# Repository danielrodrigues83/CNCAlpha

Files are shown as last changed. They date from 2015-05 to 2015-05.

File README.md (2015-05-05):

# CNCAlpha
Projeto de uma CNC para Hobby.
Iniciei este projeto com o intuito de facilitar a vida de quem está querendo começar a construir sua primeira máquina CNC.

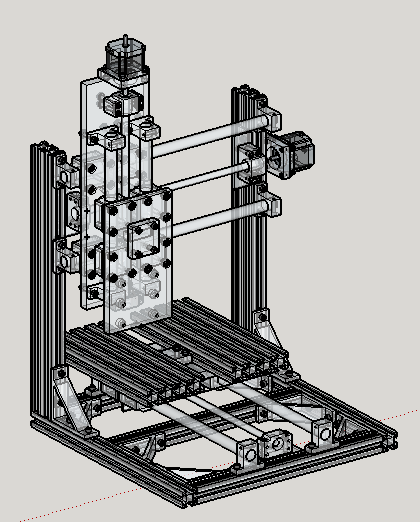
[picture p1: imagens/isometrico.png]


#Objetivos
Criar uma máquina fresadora CNC para hobby que seja capaz de usinar madeira, PCB, acrílico, PVC e demais materiais macios.
Em uma outra etapa pretendo ter um modelo que seja capaz de usinar metais macios, como por exemplo, ligas de Alumínio.

#Especificações
 - Área de trabalho: X 240mm Y 230mm Z 80mm
 - Tensão de trabalho: 24V

#Softwares Utilizados
 - <a href="http://www.sketchup.com/products/sketchup-make" target="_blank">SketchUp Make 14</a>
 - <a href="http://www.3ds.com/products-services/draftsight-cad-software/free-download/" target="_blank">DraftSight V1R3.2</a>
 - <a href="http://www.cambam.info/" target="_blank">CamBam 0.9.4</a>

#Materiais
 As quantidades de materiais estão detalhadas no arquivo <a href="CNCAlpha-BOM.xlsx" target="_blank">CNCAlpha-BOM.xlsx</a>
 - <a href="http://pt.aliexpress.com/item/1204-Rolled-Ballscrew-set-1pcs-SFU1204-L350mm-61mm-machining-parts-1pcs-ballnut-end-machining-1set-BK10/476214507.html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" target="_blank">Fuso de esfera recirculante</a>
 - <a href="http://pt.aliexpress.com/item/Free-shipping-6pcs-SK20-20mm-Shaft-Support-CNC-Router-SH20A/1048914600.html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" target="_blank">SK20</a>
 - <a href="http://pt.aliexpress.com/item/New-4pcs-lot-Free-shipping-SC20UU-SCS20UU-20mm-Linear-Slide-Block-for-DIY-CNC-Router-linear/1267047427.html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" target="_blank">SCS20UU</a>
 - <a href="http://www.marvitubos.com.br/" target="_blank">Eixos lineares 20mm</a>
 - <a href="http://www.aliexpress.com/item/Free-Shipping-6-35mm-8mm-Stepper-Motor-Shaft-Coupler-6-35mmx8mm-flexible-shaft-couplings-3pcs-lot/32241418792.html" target="_blank">Acopladores 6,35x8mm</a>
 - <a href="http://www.casafer.com.br/produto-477-Parafuso+Allen+com+Cabeca+(DIN912)" target="_blank">Parafusos allen cabeça cilíndrica(DIN912)</a>
 - <a href="http://www.lojaforseti.com/produtos-index/categorias/1167688/perfil.html" target="_blank">Perfis de Alumínio 30x30mm e 30x60mm</a> 
 - <a href="http://www.lojaforseti.com/produtos-index/categorias/1434667/cantoneiras.html" target="_blank">Cantoneiras</a> 
 - <a href="http://www.lojaforseti.com/produtos-index/categorias/1506114/porcas.html" target="_blank">Porcas para os perfis de alumínio</a> 
 - <a href="http://www.aliexpress.com/item/Free-shipping-CNC-3-AXIS-Stepper-Driver-Board-Controller-TB6560-3-5A-SM362-CF/520301796.html" target="_blank">Placa controladora de 3 eixos</a>
 - <a href="http://www.aliexpress.com/store/product/3PCS-NEMA23-270-Oz-in-CNC-stepper-motor-stepping-motor-3-0A/907217_541699816.html" target="_blank">Motores Nema 23</a>
 - <a href="http://produto.mercadolivre.com.br/MLB-651414629-fonte-chaveada-12v-30a-360w-bivolt-p-cameras-fita-led-cftv-_JM" target="_blank">Fonte 12V 30A</a>
 - <a href="http://www.soldafria.com.br/chave-micro-switch-c-30_267.html" target="_blank">Endstops, fios</a>
 - <a href="http://www.aliexpress.com/item/2pcs-CNC-Emergency-Stop-Pushbutton-Switch-LAY37-11ZS/32331147402.html" target="_blank">Botão de emergência</a>
 - <a href="http://www.ebay.com/itm/ER11-Spindle-for-Sable-2015-SPD-ER11-ENGRAVER-mill-PCBs-engraving-/201337995174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" target="_blank">Spindle</a>

#Instruções para fabricação
 Os arquivos contendo os desenhos das peças que precisam ser fabricadas estão na pasta <a href="desenhos2D" target="_blank">desenho2D</a>.
 O objetivo é utilizar estes arquivos como base para a criação dos Gcodes, por isso não foram incluídos cotas e símbolos.
 Os arquivos Gcodes serão salvos na pasta <a href="cam" target="_blank">cam</a>
 Serão disponibilizados, também, os arquivos editáveis do CamBam.
 
#Observações
 - Tentei fazer todas as peças a serem fabricadas com o dimensional que fosse possível usinar através dela.
 - A mesa do eixo Y, devido ao seu tamanho, foi necessário realizar a usinagem em duas etapas.
 - Serão utilizadas duas fontes, ligadas em série, de 12V 30A para fornecer 24V aos motores e ao spindle.
 - Estou tentando fazer algo organizado e que seja útil para quem queira iniciar neste hobby, portanto qualquer ajuda e sugestão construtiva são muito bem vindos.

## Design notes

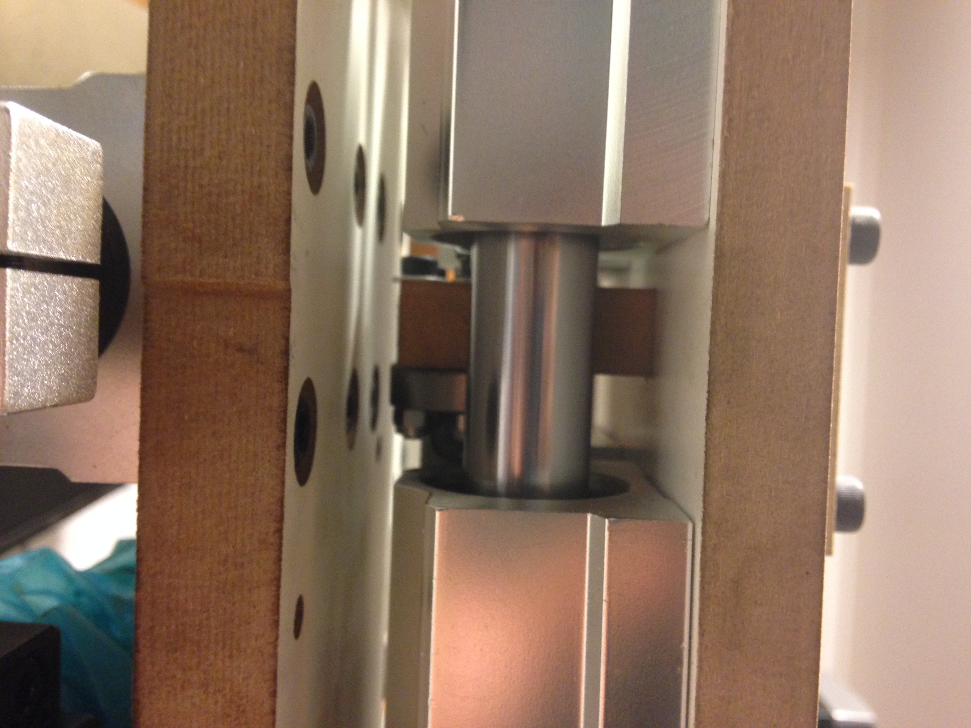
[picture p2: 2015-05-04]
fotos/2015-04-30 17.04.00.jpg

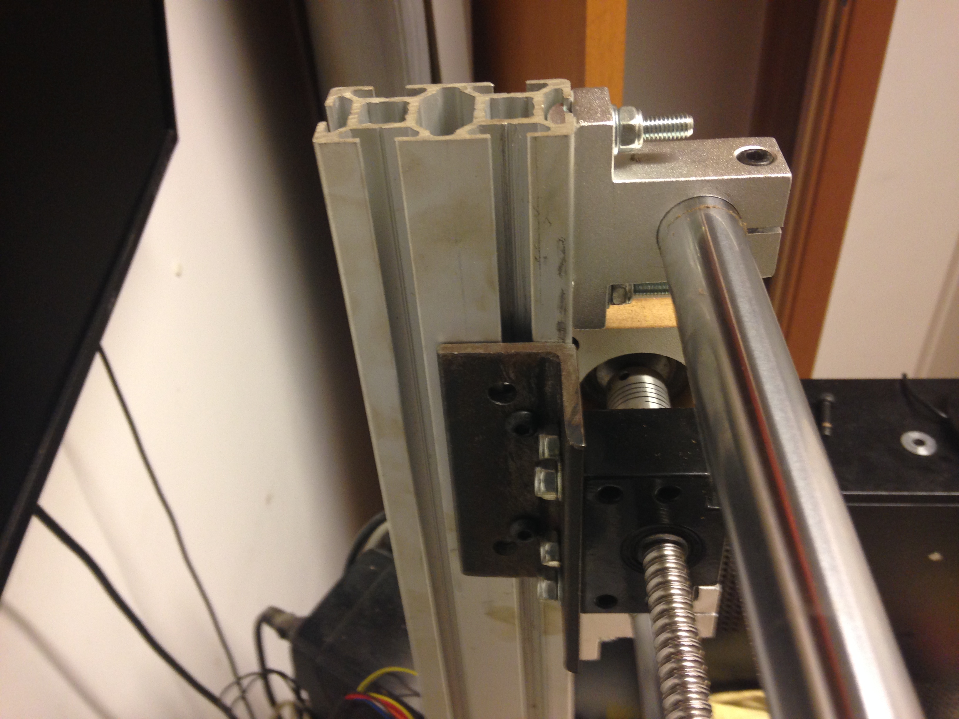
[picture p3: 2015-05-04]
fotos/2015-04-30 17.04.11.jpg

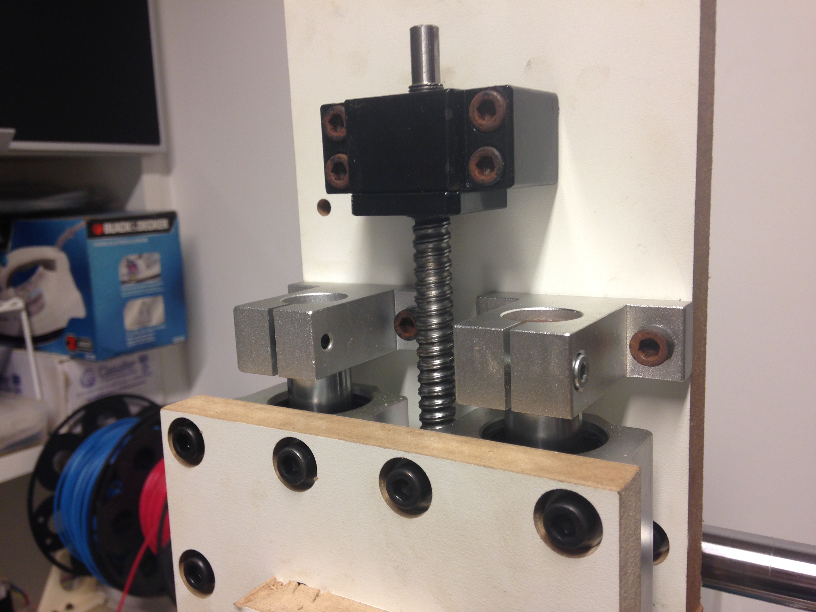
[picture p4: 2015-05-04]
fotos/2015-04-30 17.03.50.jpg

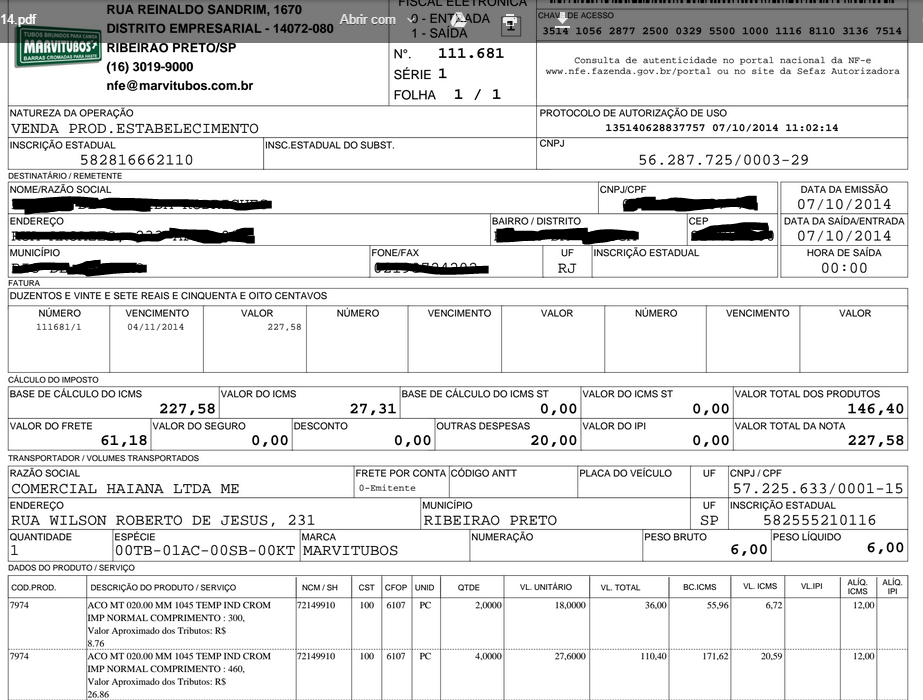
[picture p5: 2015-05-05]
imagens/nota-fiscal-marvitubos.PNG

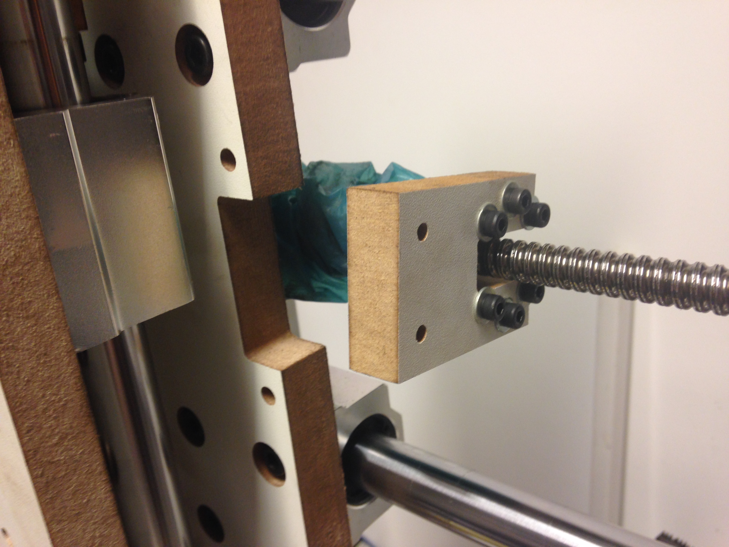
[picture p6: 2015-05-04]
fotos/2015-04-30 17.03.44.jpg

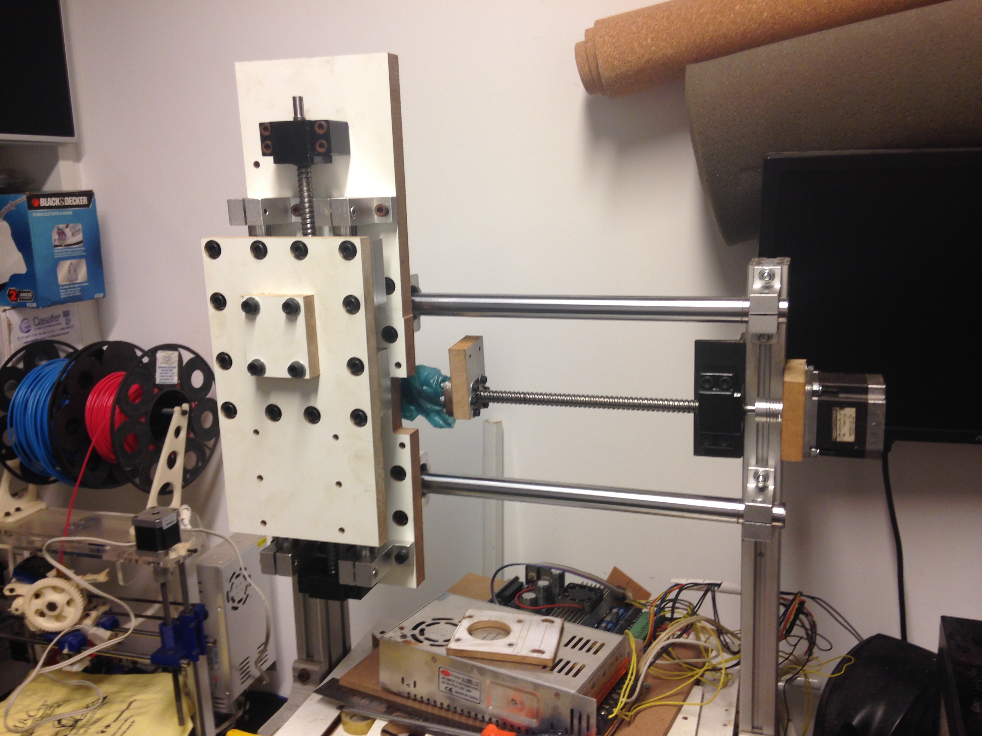
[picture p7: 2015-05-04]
fotos/2015-04-30 17.03.37.jpg

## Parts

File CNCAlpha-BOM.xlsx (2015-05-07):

Lista de Materiais
 | Item | Quantidade | Local | Valor China | Valor Brasil | valor(menor) referencia | valor referencia total | valor Brasil Total
Movimento
 | BF10 | 3 |  |  |  | R$0.00
 | BK10 | 3 |  |  |  | R$0.00
 | Fuso com castanha SFU1204 30cm | 3 | CHINA | R$235.00 | R$320.00 | R$235.00 | R$705.00 | R$960.00
 | SCS20UU | 12 | CHINA | R$20.00 | R$40.00 | R$20.00 | R$240.00 | R$480.00
 | SK20 | 12 | CHINA | R$8.50 | R$24.00 | R$8.50 | R$102.00 | R$288.00
 | Eixo diametro 20mm compr. 450mm | 4 | BRASIL |  | R$27.60 | R$27.60 | R$110.40 | R$110.40
 | Eixo diametro 20mm compr. 300mm | 2 | BRASIL |  | R$27.98 | R$27.98 | R$55.96 | R$55.96
 | Acoplador eixos 6,35 x 8mm x 25mm | 3 | CHINA | R$15.00 | R$15.00 | R$15.00 | R$45.00 | R$45.00
Estrutura
 | cantoneira100x100x30 | 8 | BRASIL |  | R$13.00 | R$13.00 | R$104.00 | R$104.00
 | Perfil T-slot 30x30 compr. 400mm | 3 | BRASIL |  | R$11.20 | R$11.20 | R$33.60 | R$33.60
 | Perfil T-slot 30x30 compr. 460mm | 2 | BRASIL |  | R$12.88 | R$12.88 | R$25.76 | R$25.76
 | Perfil T-slot 60x30 compr. 500mm | 2 | BRASIL |  | R$24.00 | R$24.00 | R$48.00 | R$48.00
 | Perfil T-slot 60x30 compr. 300mm | 4 | BRASIL |  | R$14.40 | R$14.40 | R$57.60 | R$57.60
Parafusos
 | DIN912 M4X30+NYLOC | 18 | BRASIL |  | R$0.70 | R$0.70 | R$12.60 | R$12.60
 | DIN912 M5X20+NYLOC | 12 | BRASIL |  | R$0.70 | R$0.70 | R$8.40 | R$8.40
 | DIN 912 M6x10 | 8 | BRASIL |  | R$0.70 | R$0.70 | R$5.60 | R$5.60
 | DIN 912 M6x16 | 60 | BRASIL |  | R$0.70 | R$0.70 | R$42.00 | R$42.00
 | DIN 912 M6x20+ARRUELA | 32 | BRASIL |  | R$0.70 | R$0.70 | R$22.40 | R$22.40
 | DIN 912 M6x25+ARRUELA+NYLOC | 2 | BRASIL |  | R$0.70 | R$0.70 | R$1.40 | R$1.40
 | DIN 912 M6x35+ARRUELA+NYLOC | 12 | BRASIL |  | R$0.70 | R$0.70 | R$8.40 | R$8.40
 | DIN912 M6X40+ARRUELA+NYLOC | 12 | BRASIL |  | R$0.70 | R$0.70 | R$8.40 | R$8.40
 | DIN912 M6X40 | 4 | BRASIL |  | R$0.70 | R$0.70 | R$2.80 | R$2.80
 | DIN912 M6X50+ARRUELA+NYLOC | 6 | BRASIL |  | R$0.70 | R$0.70 | R$4.20 | R$4.20
 | Porca para Perfil T-slot 30 - M6 | 72 | BRASIL |  | R$1.65 | R$1.65 | R$118.80 | R$118.80
Fabricação
 | Fabricar-cantoneira-1/2" | 1 | BRASIL |  | R$5.00 | R$5.00 | R$5.00 | R$5.00
 | Fabricar-cantoreira-1/8"x1.1/2"x100-furo-duplo | 2 | BRASIL |  | R$20.00 | R$20.00 | R$40.00 | R$40.00
 | Fabricar-cantoreira-1/8"x1.1/2"x100-furo-simples | 2 | BRASIL |  | R$20.00 | R$20.00 | R$40.00 | R$40.00
 | Fabricar-X-mesa | 1 | BRASIL |  | em cotação | em cotação
 | Fabricar-X-trava-castanha-2 | 1 | BRASIL |  | em cotação | em cotação
 | Fabricar-X-trava-castanha | 1 | BRASIL |  | em cotação | em cotação
 | Fabricar-Y-trava-castanha | 1 | BRASIL |  | em cotação | em cotação
 | Fabricar-Z-mesa | 1 | BRASIL |  | em cotação | em cotação
 | Fabricar-Z-trava-castanha-2 | 1 | BRASIL |  | em cotação | em cotação
 | Fabricar-Z-trava-castanha | 1 | BRASIL |  | em cotação | em cotação
 | Fabricar-suporte-motor-XY | 2 | BRASIL |  | em cotação | em cotação
 | Fabricar-suporte-motor-Z | 1 | BRASIL |  | em cotação | em cotação
 | Fabricar-Y-mesa | 1 | BRASIL |  | em cotação | em cotação
Eletrônica
 | Motores Nema 23 15Kgf*cm | 3 | CHINA | R$135.00 | R$60.00 | R$135.00 | R$405.00 | R$180.00
 | Placa controladora de 3eixos TB6560 | 1 | CHINA | R$125.00 | R$280.00 | R$125.00 | R$125.00 | R$280.00
 | Fonte 12v 30A | 2 | BRASIL |  | R$57.00 | R$57.00 | R$114.00 | R$114.00
 | End stop switch | 6 | BRASIL |  | R$5.00 | R$5.00 | R$30.00 | R$30.00
 | Botao de parada | 1 | CHINA | R$25.00 | R$17.00 | R$17.00 | R$17.00 | R$17.00
 | Spindle | 1 | CHINA | R$305.00 | R$350.00 | R$305.00 | R$305.00 | R$350.00
 |  |  |  |  |  | TOTAL | R$2843.32 | R$3499.32

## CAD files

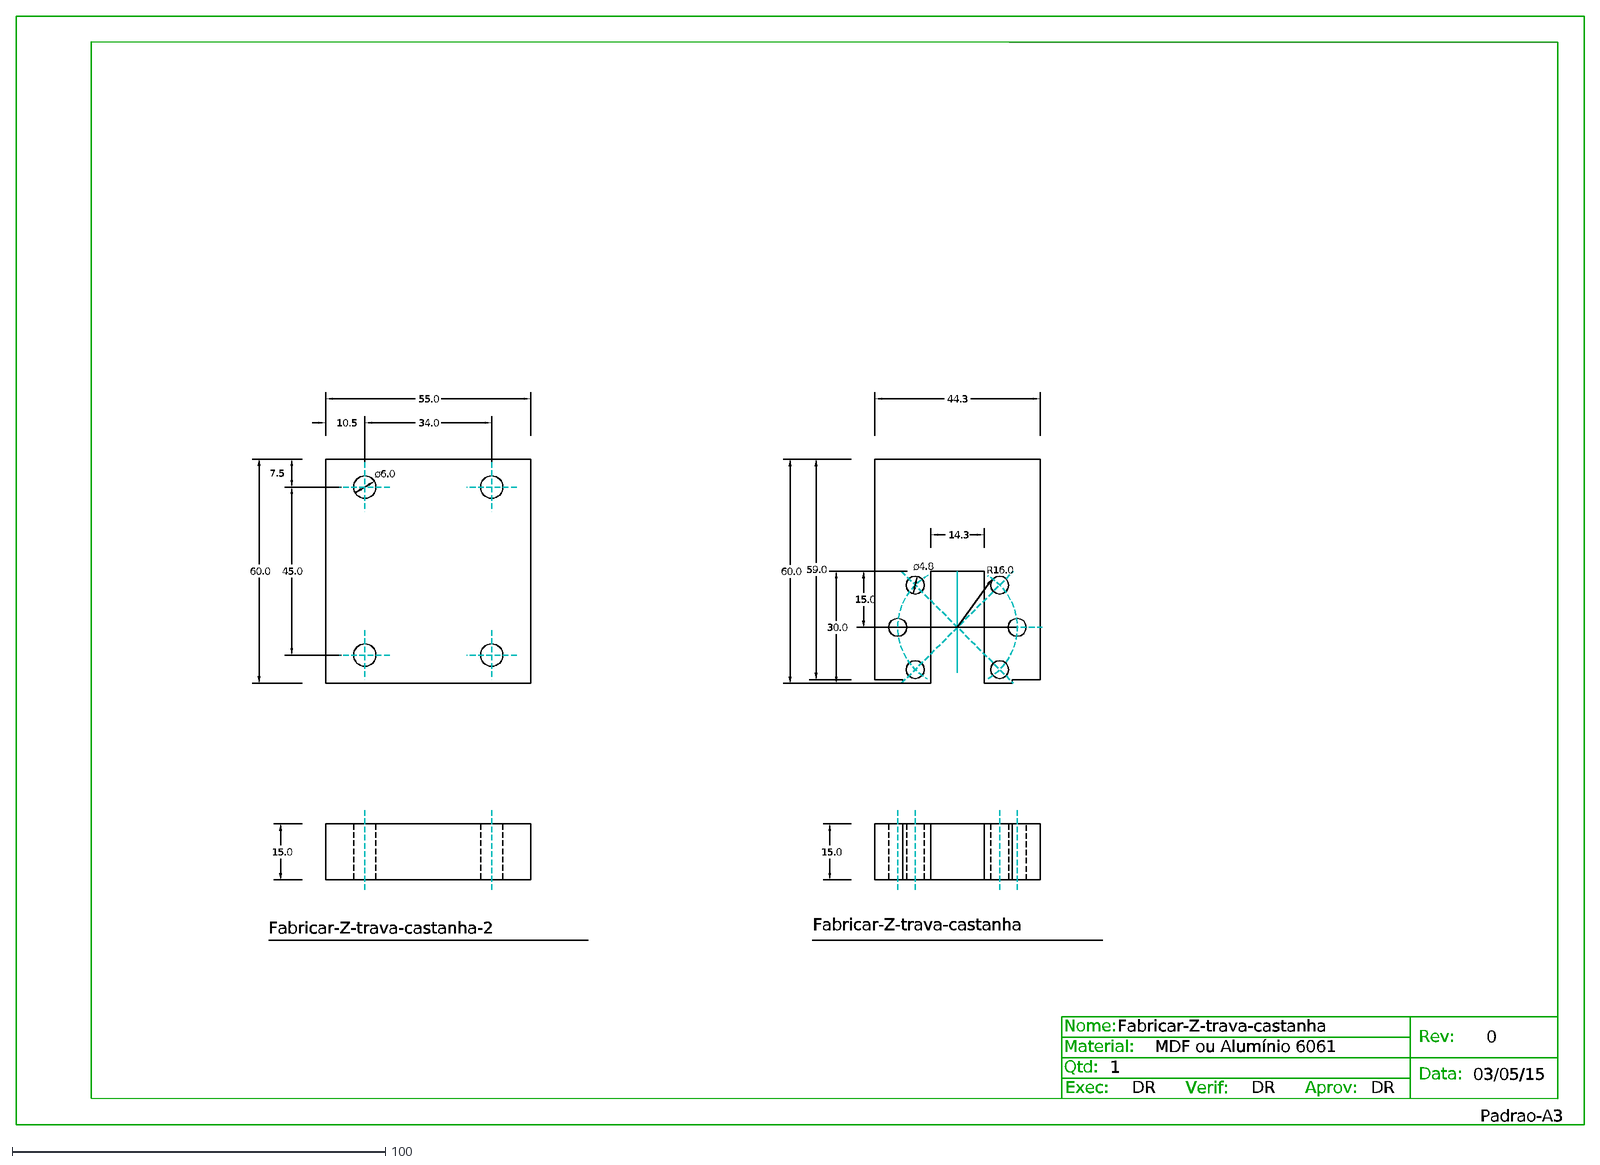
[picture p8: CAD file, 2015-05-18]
desenhos2D/Fabricar-Z-trava-castanha.dxf
Padrao-A3
Fabricar-Z-trava-castanha-2
Fabricar-Z-trava-castanha
Verif:
Exec:
Material:
Rev:
Data:
Aprov:
DR
0
03/05/15
MDF ou Alumínio 6061
Nome:
Qtd:
1
R16.0
14.3
60.0
59.0
30.0
15.0
44.3
55.0
10.5
34.0
7.5
45.0
ø4.8
ø6.0

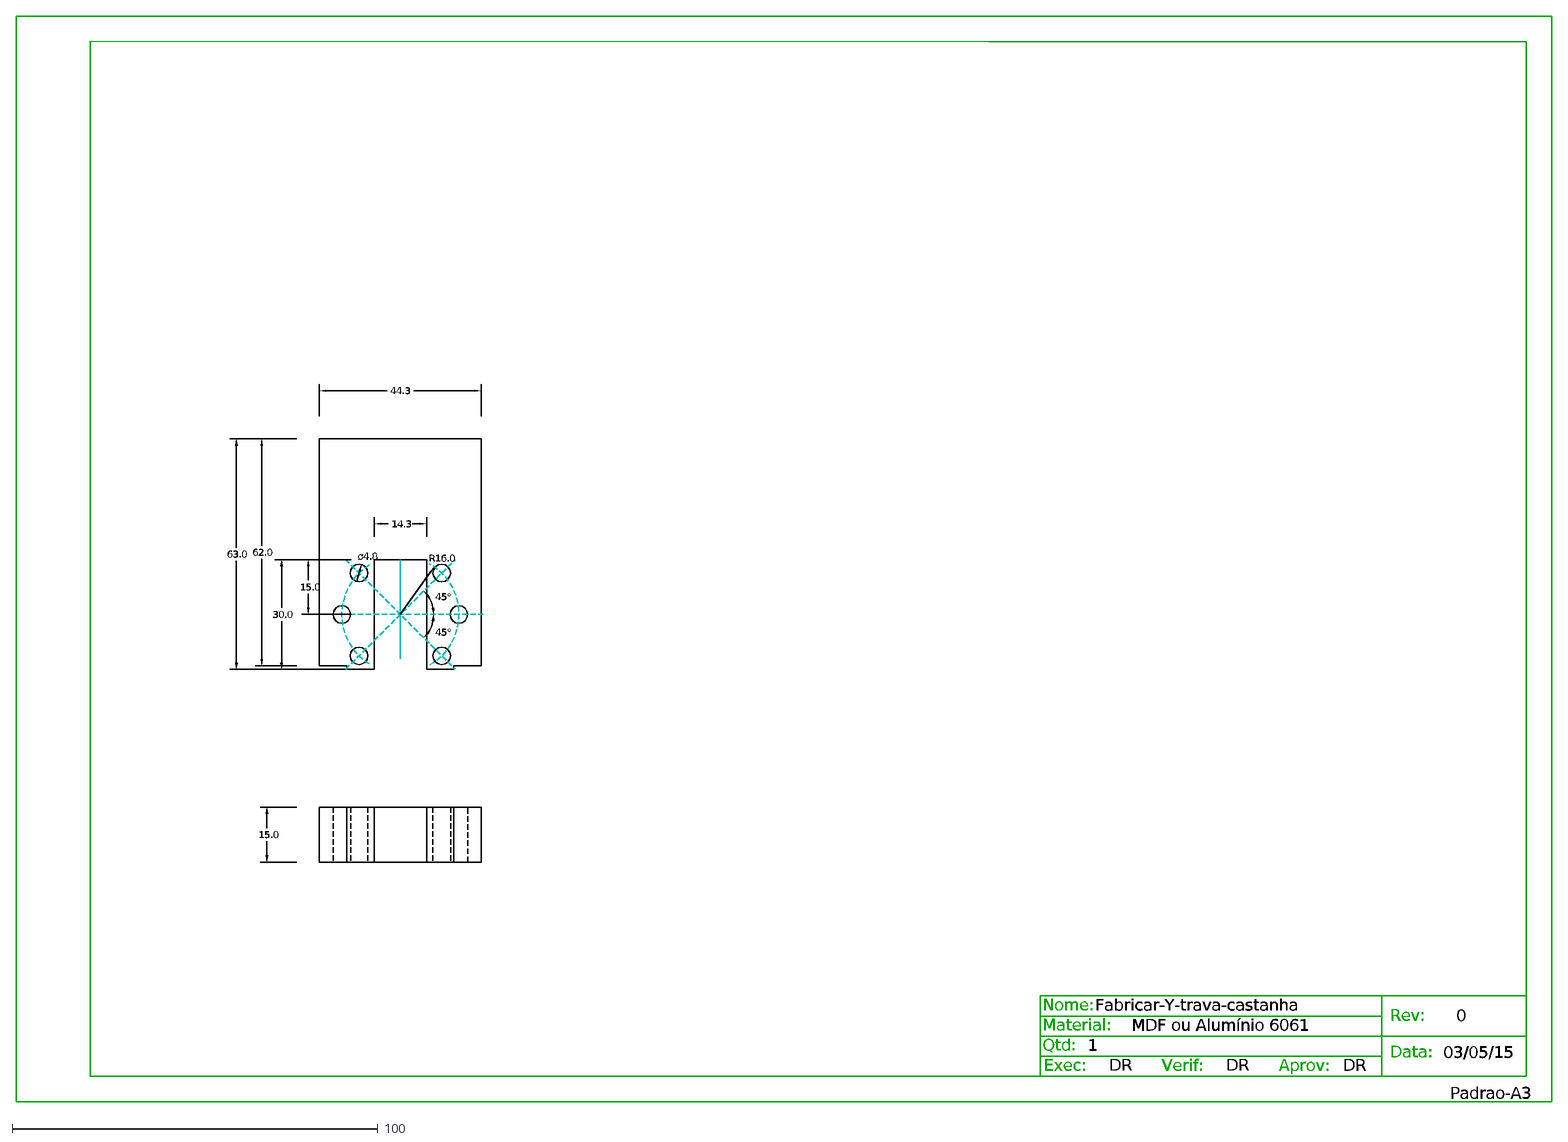
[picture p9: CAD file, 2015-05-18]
desenhos2D/Fabricar-Y-trava-castanha.dxf
Padrao-A3
Verif:
Exec:
Material:
Rev:
Data:
Aprov:
DR
0
03/05/15
MDF ou Alumínio 6061
Fabricar-Y-trava-castanha
Nome:
Qtd:
1
44.3
63.0
62.0
30.0
14.3
45°
R16.0
ø4.8
15.0

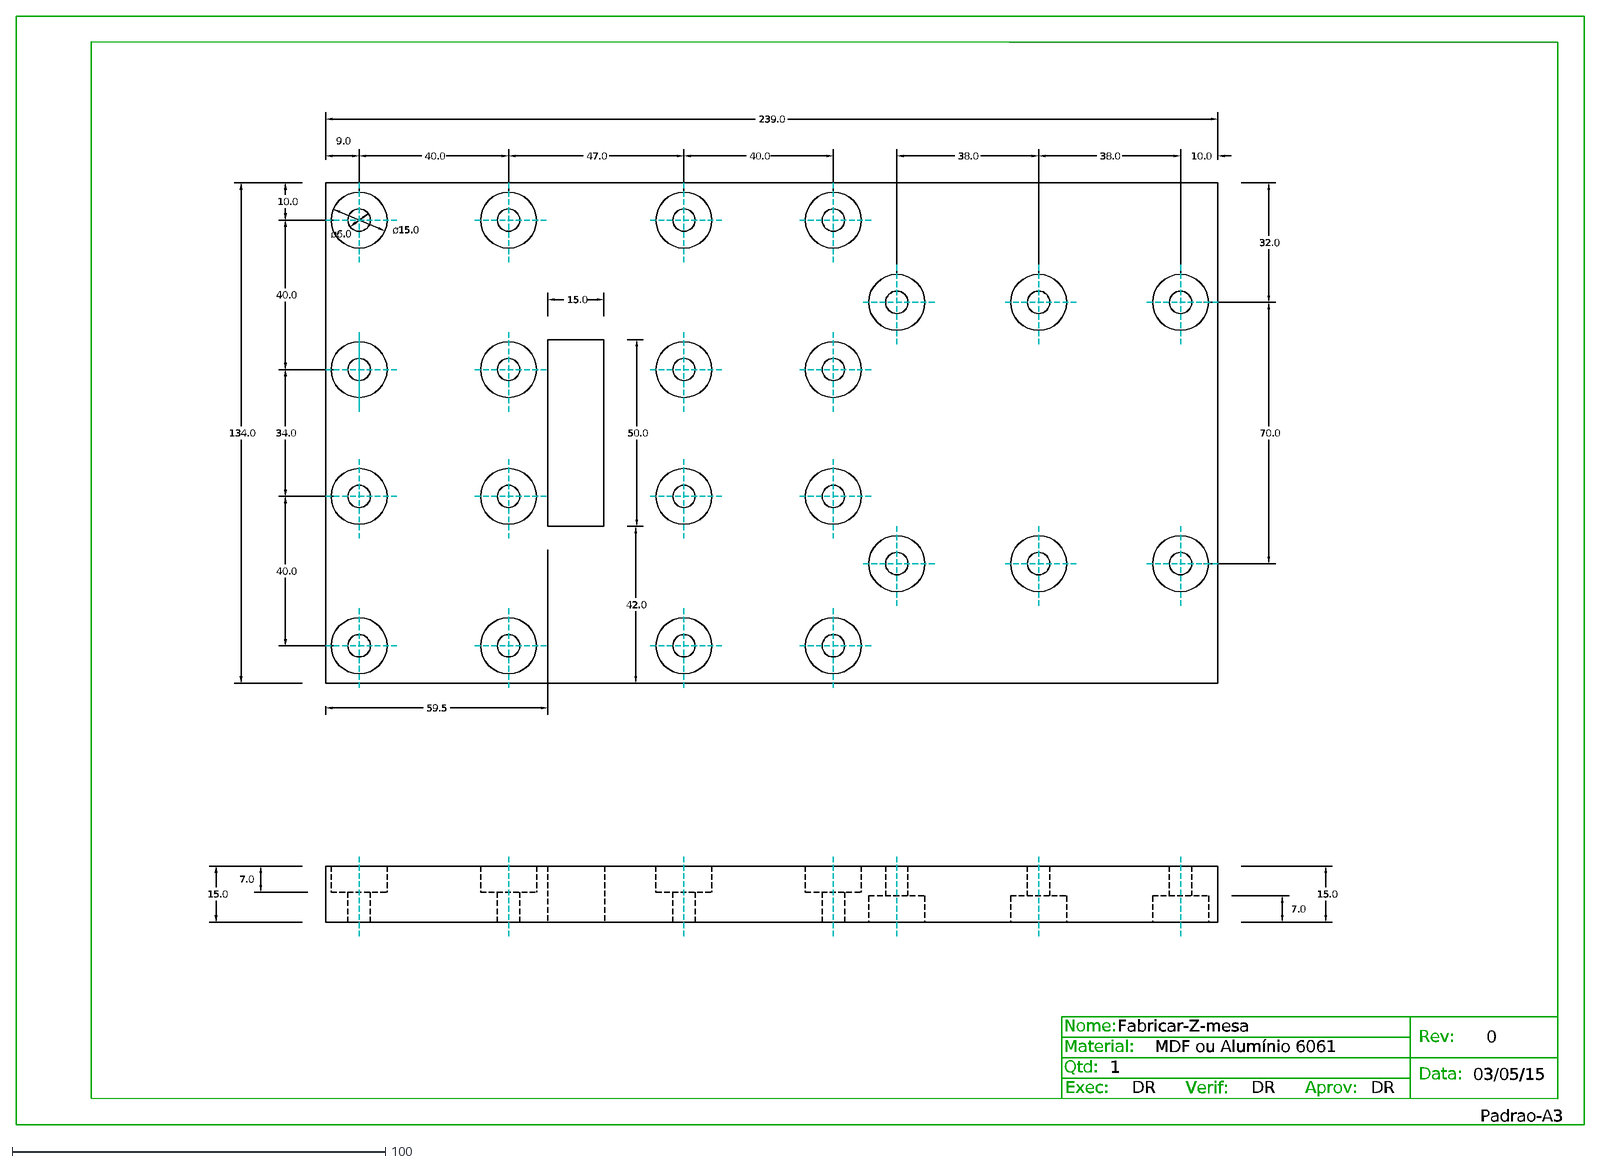
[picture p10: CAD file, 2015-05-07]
desenhos2D/Fabricar-Z-mesa.dxf
Padrao-A3
Verif:
Exec:
Material:
Rev:
Data:
Aprov:
DR
0
03/05/15
MDF ou Alumínio 6061
Fabricar-Z-mesa
Nome:
Qtd:
1
9.0
40.0
47.0
10.0
34.0
50.0
15.0
ø6.0
ø15.0
239.0
134.0
59.5
42.0
38.0
32.0
70.0
7.0

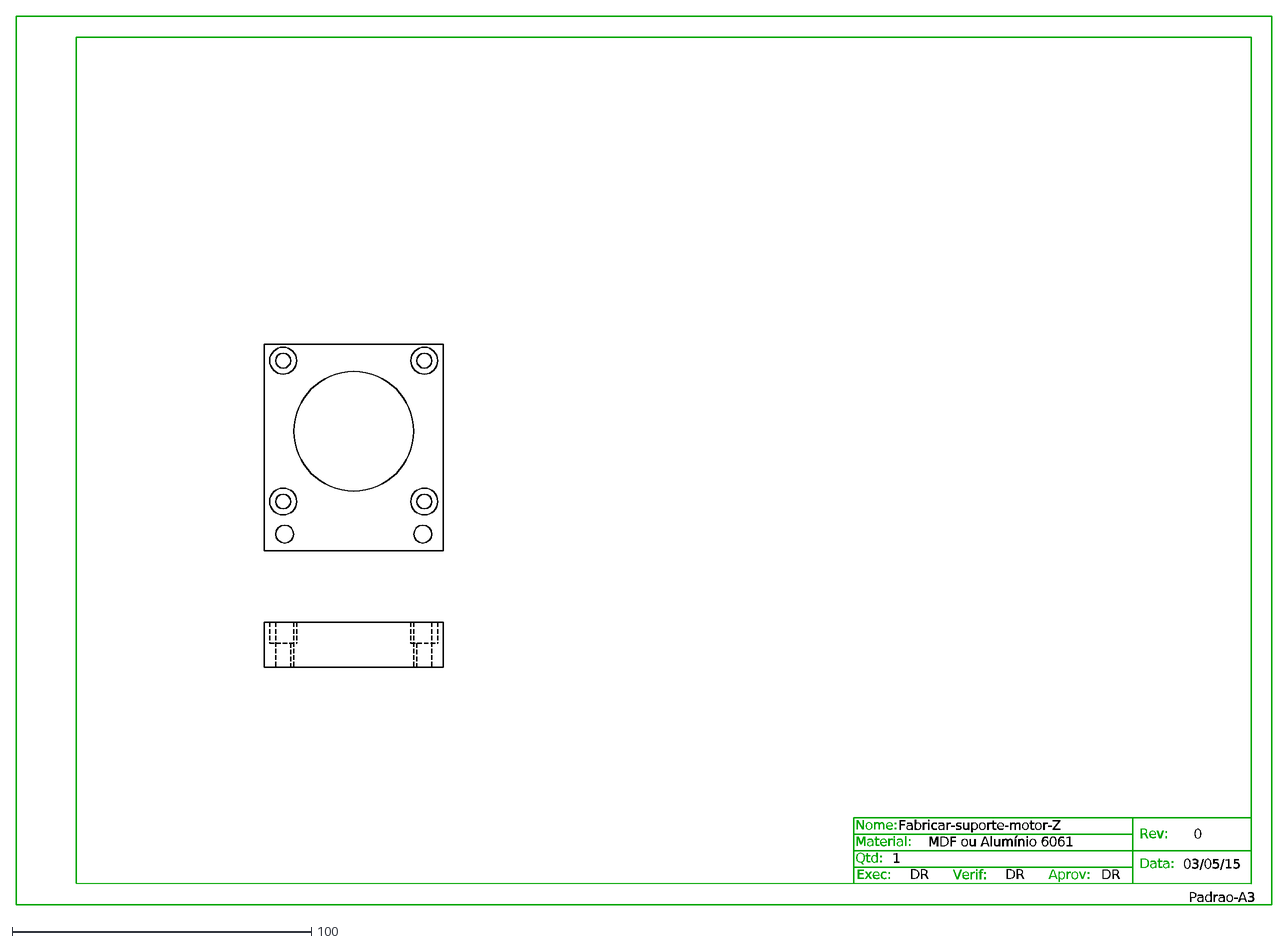
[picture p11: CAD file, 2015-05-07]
desenhos2D/Fabricar-suporte-motor-Z.dxf
Padrao-A3
Verif:
Exec:
Material:
Rev:
Data:
Aprov:
DR
0
03/05/15
MDF ou Alumínio 6061
Fabricar-suporte-motor-Z
Nome:
Qtd:
1

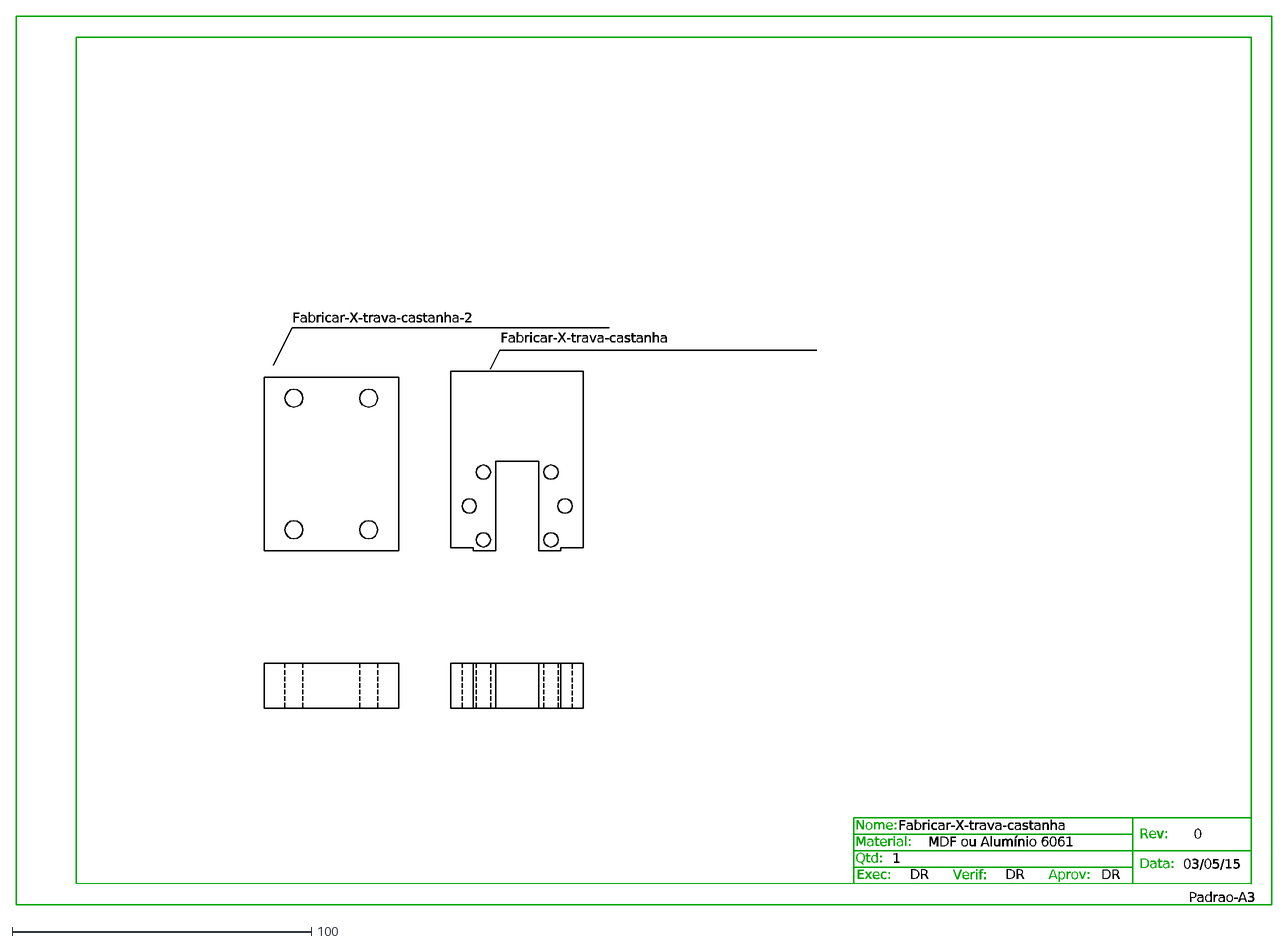
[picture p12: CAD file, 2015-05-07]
desenhos2D/Fabricar-X-trava-castanha.dxf
Padrao-A3
Fabricar-X-trava-castanha-2
Fabricar-X-trava-castanha
Verif:
Exec:
Material:
Rev:
Data:
Aprov:
DR
0
03/05/15
MDF ou Alumínio 6061
Nome:
Qtd:
1

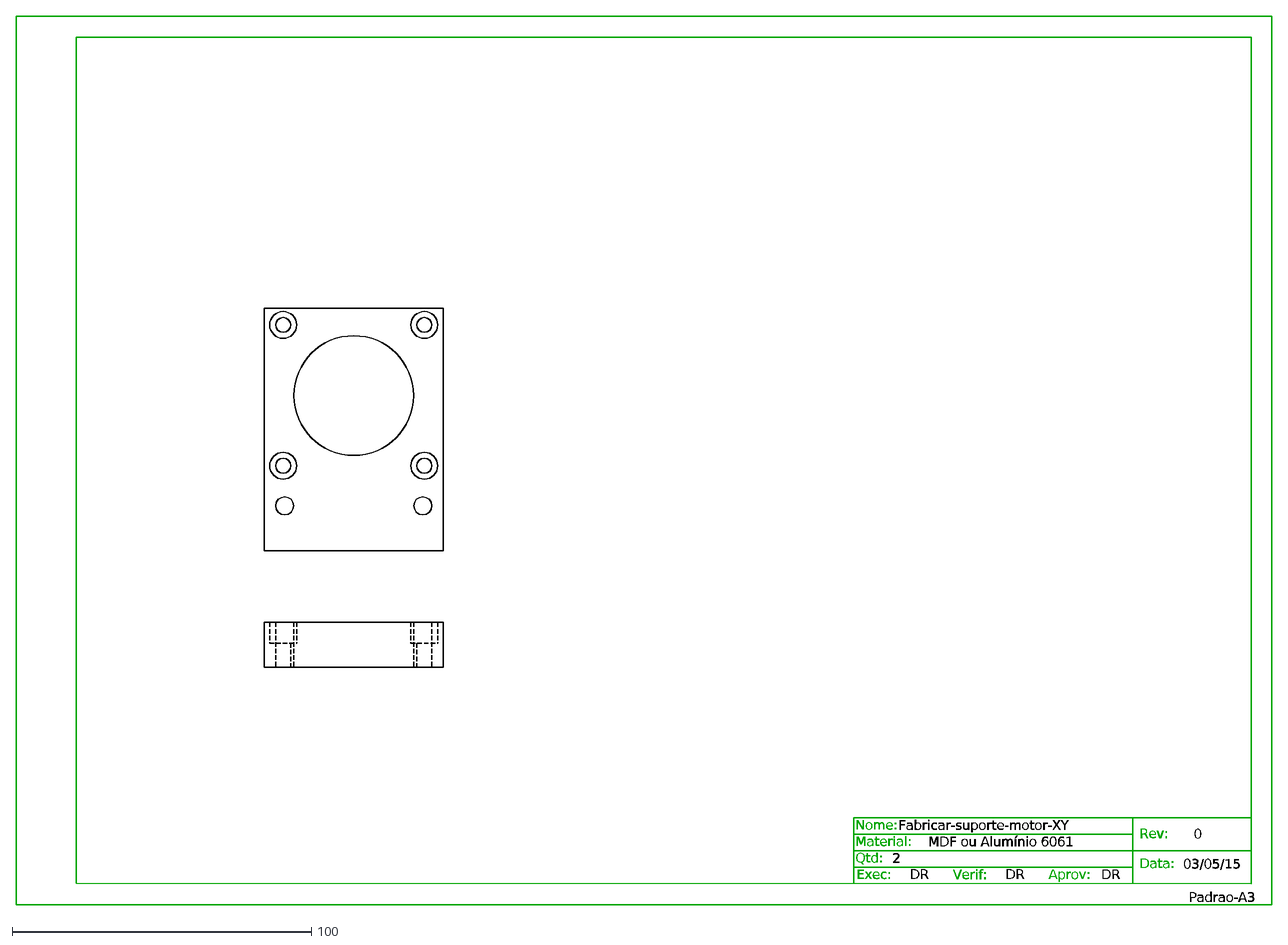
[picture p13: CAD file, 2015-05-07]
desenhos2D/Fabricar-suporte-motor-XY.dxf
Verif:
Exec:
Material:
Rev:
Data:
Aprov:
DR
0
03/05/15
MDF ou Alumínio 6061
Padrao-A3
Fabricar-suporte-motor-XY
Nome:
Qtd:
2

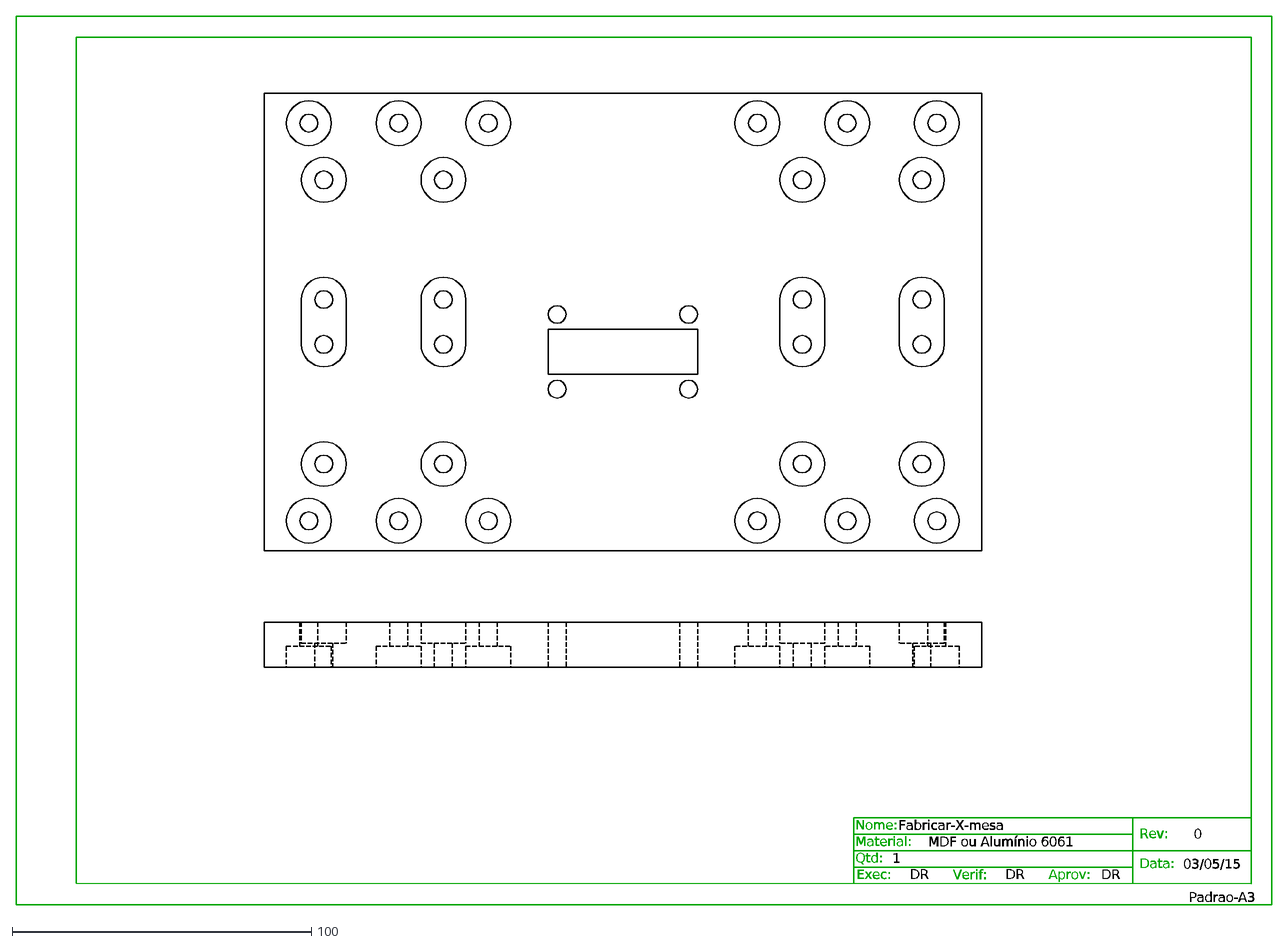
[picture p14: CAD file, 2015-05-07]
desenhos2D/Fabricar-X-mesa.dxf
Padrao-A3
0
Verif:
Exec:
Material:
Rev:
Data:
Aprov:
DR
03/05/15
MDF ou Alumínio 6061
Fabricar-X-mesa
Nome:
Qtd:
1

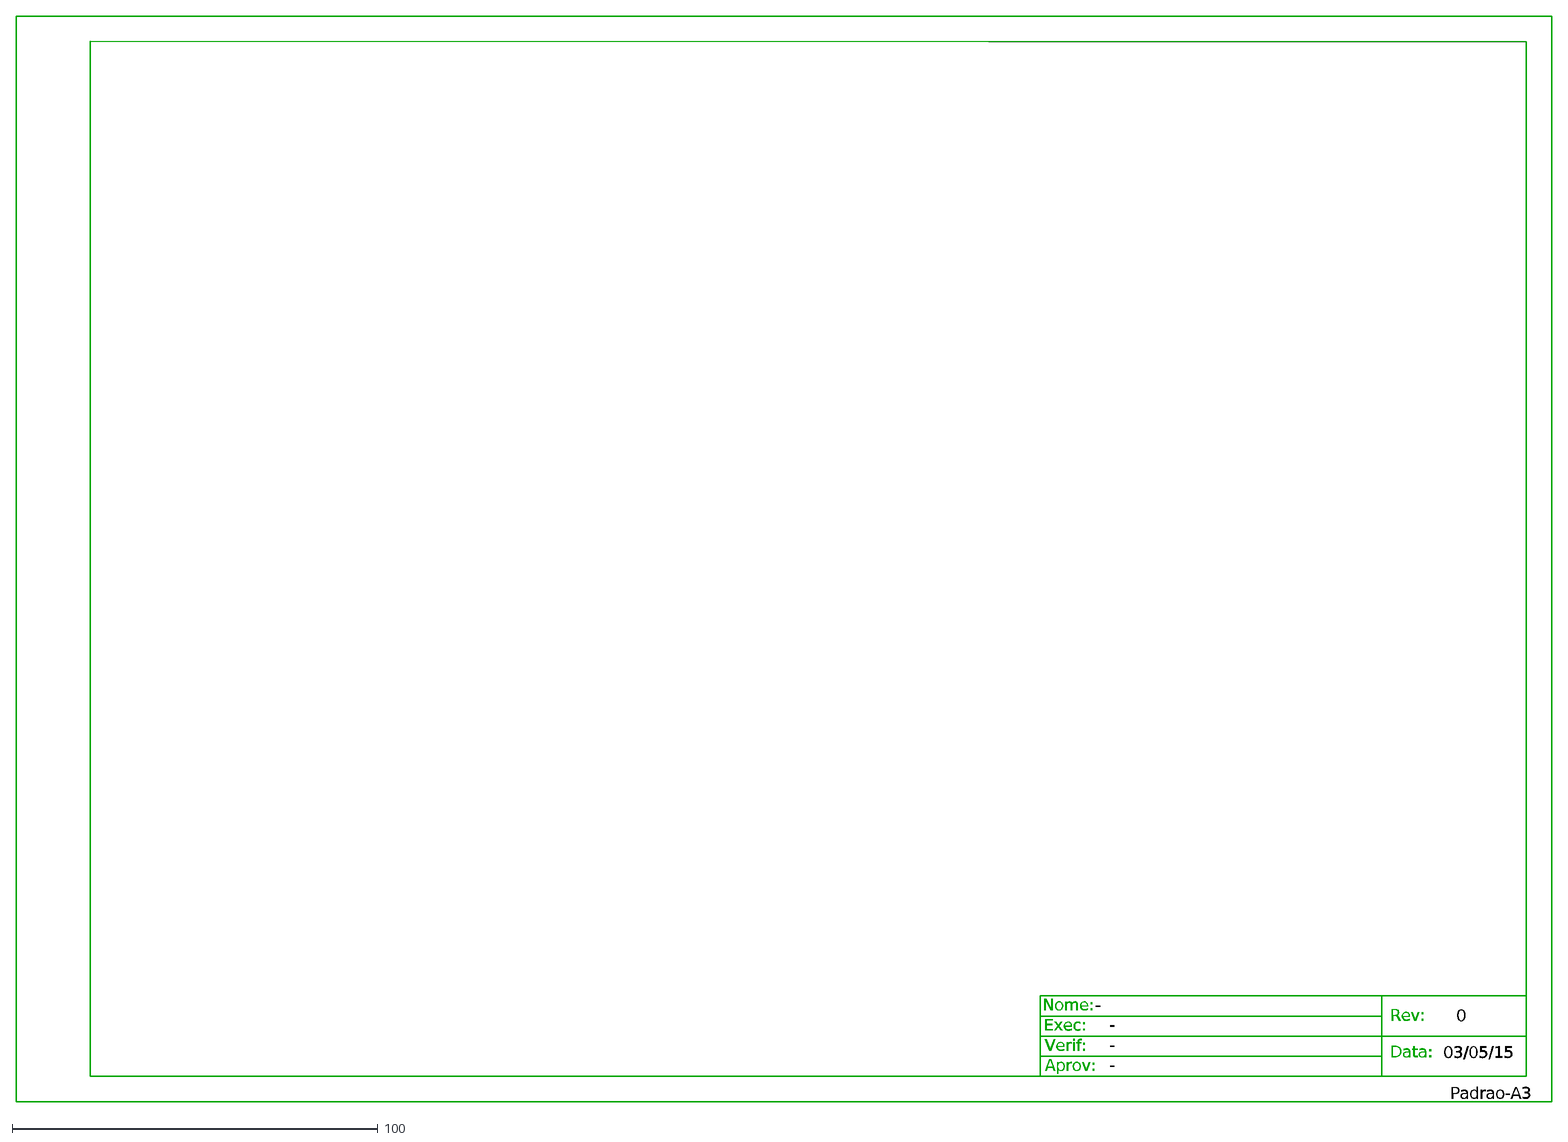
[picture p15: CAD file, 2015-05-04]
desenhos2D/Padrao-A3.dxf
Verif:
Exec:
Nome:
Rev:
Data:
Aprov:
-
0
03/05/15
Padrao-A3

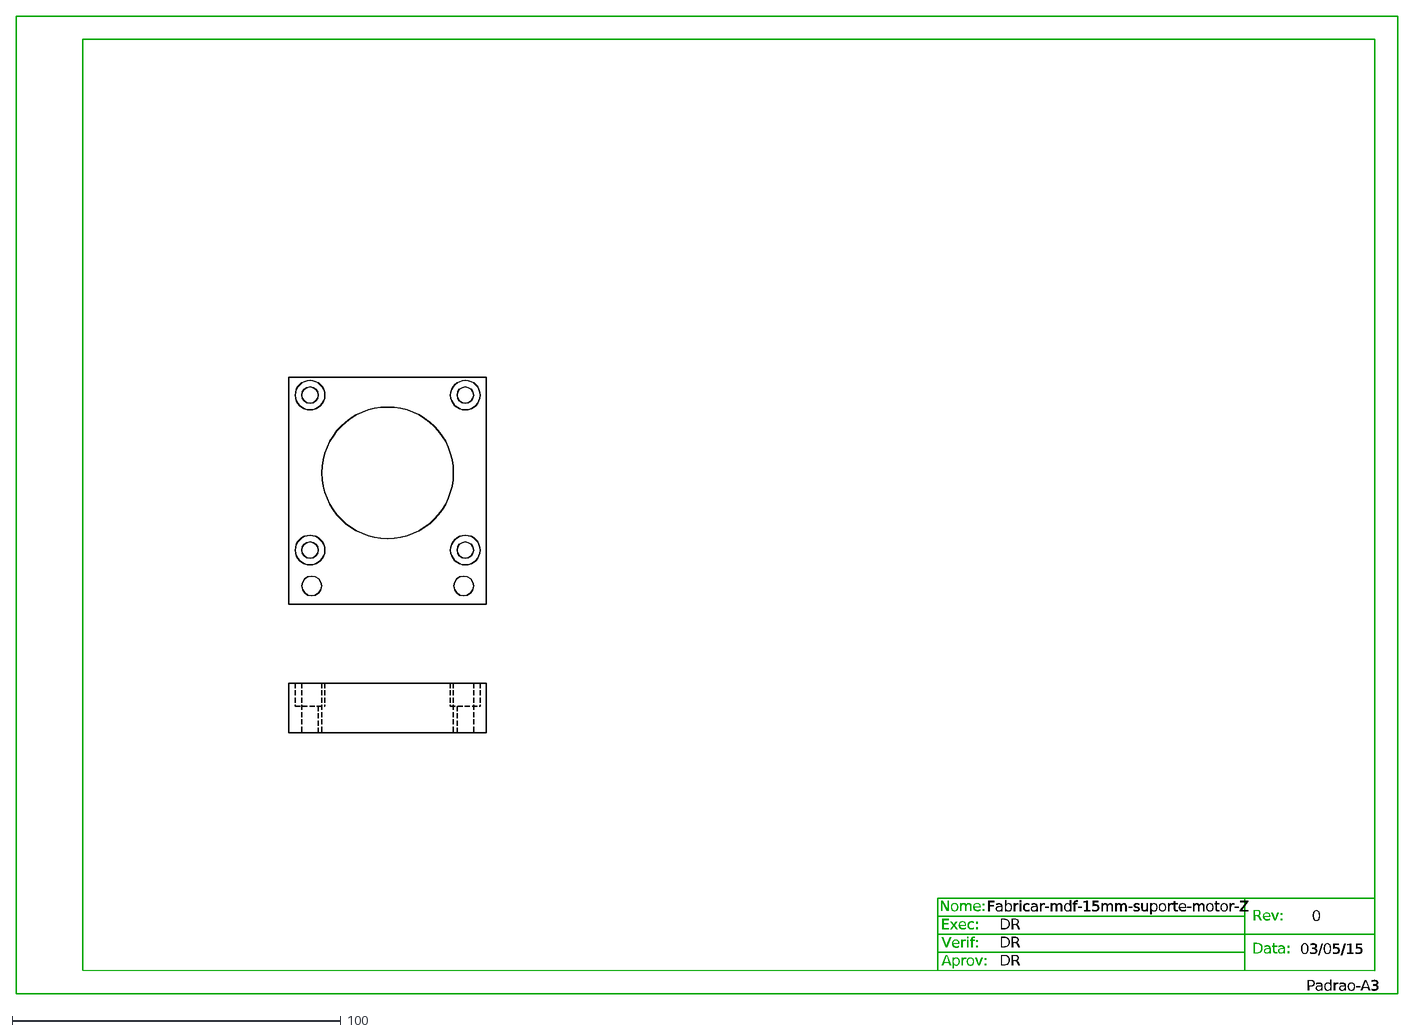
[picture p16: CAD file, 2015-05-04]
desenhos2D/Fabricar-mdf-15mm-suporte-motor-Z.dxf
Verif:
Exec:
Nome:
Rev:
Data:
Aprov:
DR
0
03/05/15
Fabricar-mdf-15mm-suporte-motor-Z
Padrao-A3

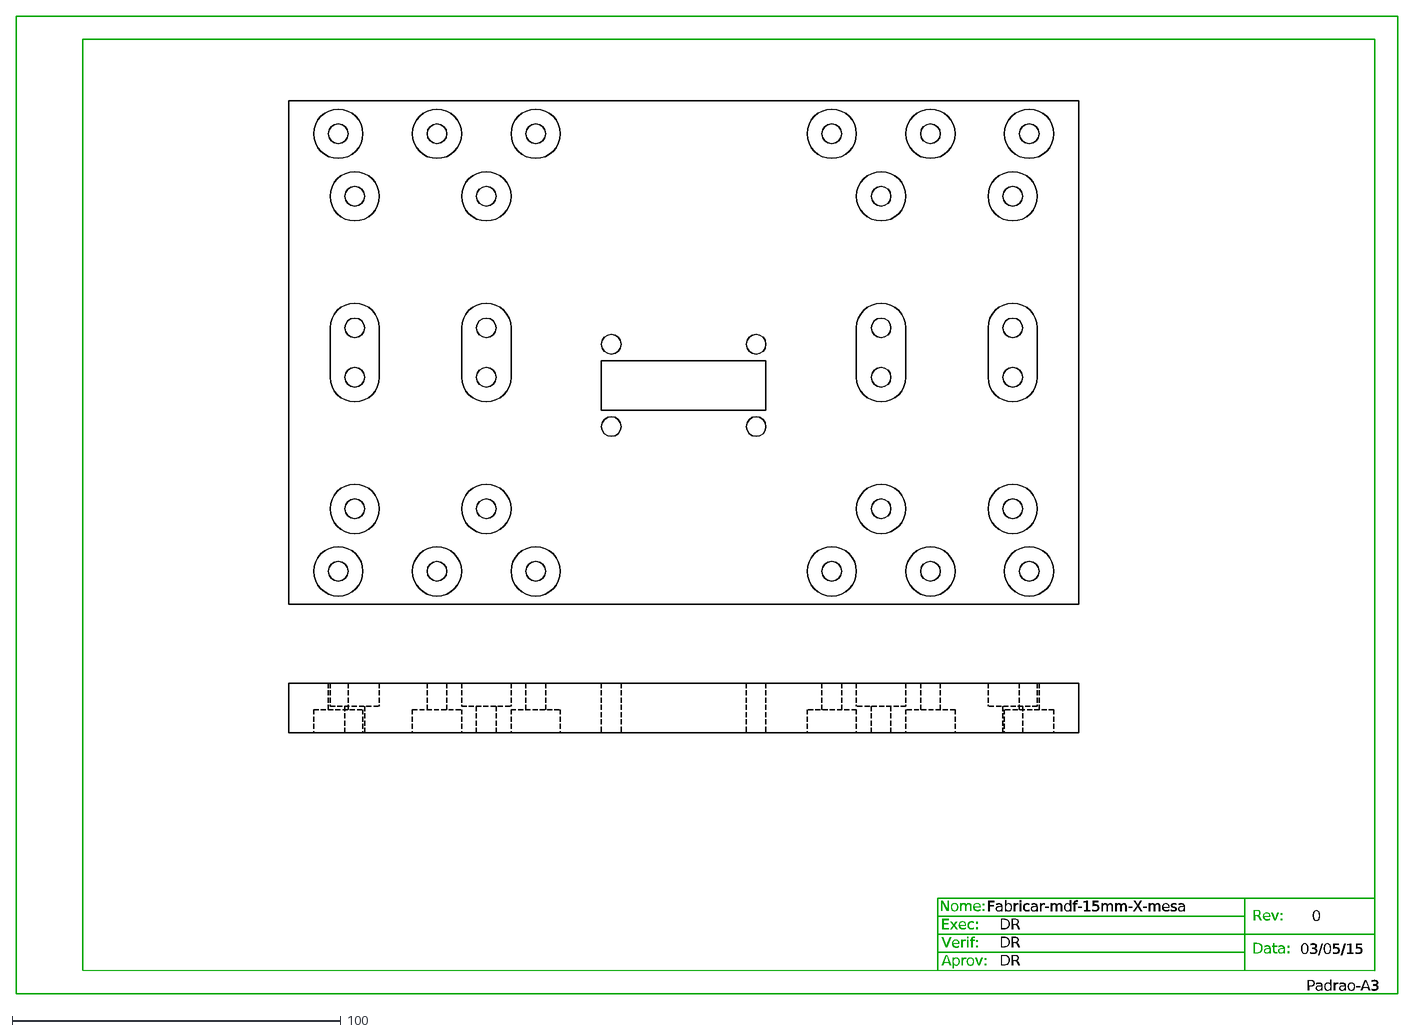
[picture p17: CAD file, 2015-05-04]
desenhos2D/Fabricar-mdf-15mm-X-mesa.dxf
Verif:
Exec:
Nome:
Rev:
Data:
Aprov:
DR
0
03/05/15
Fabricar-mdf-15mm-X-mesa
Padrao-A3

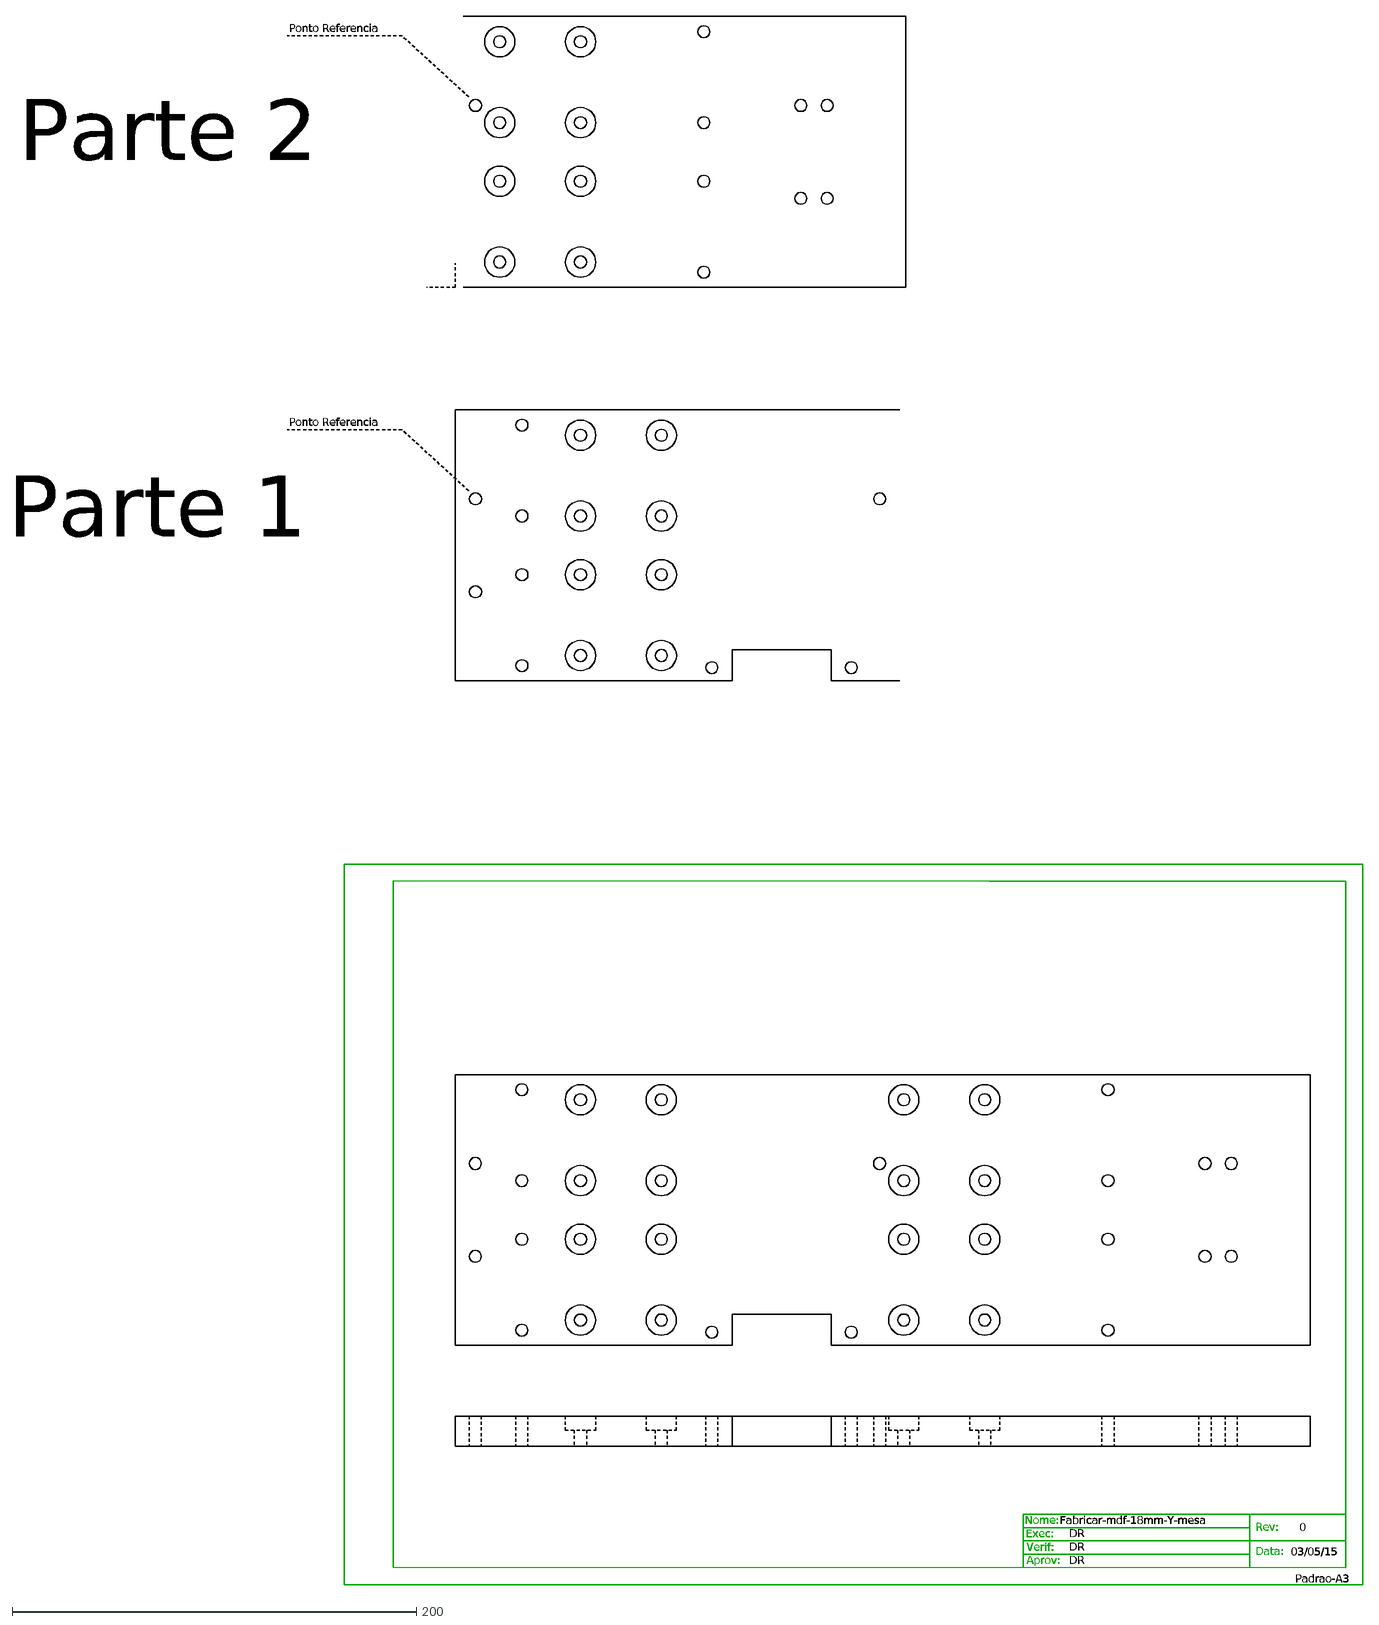
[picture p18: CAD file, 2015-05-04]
desenhos2D/Fabricar-mdf-18mm-Y-mesa.dxf
Verif:
Exec:
Nome:
Rev:
Data:
Aprov:
DR
0
03/05/15
Fabricar-mdf-18mm-Y-mesa
Padrao-A3
Parte 1
Parte 2
Ponto Referencia

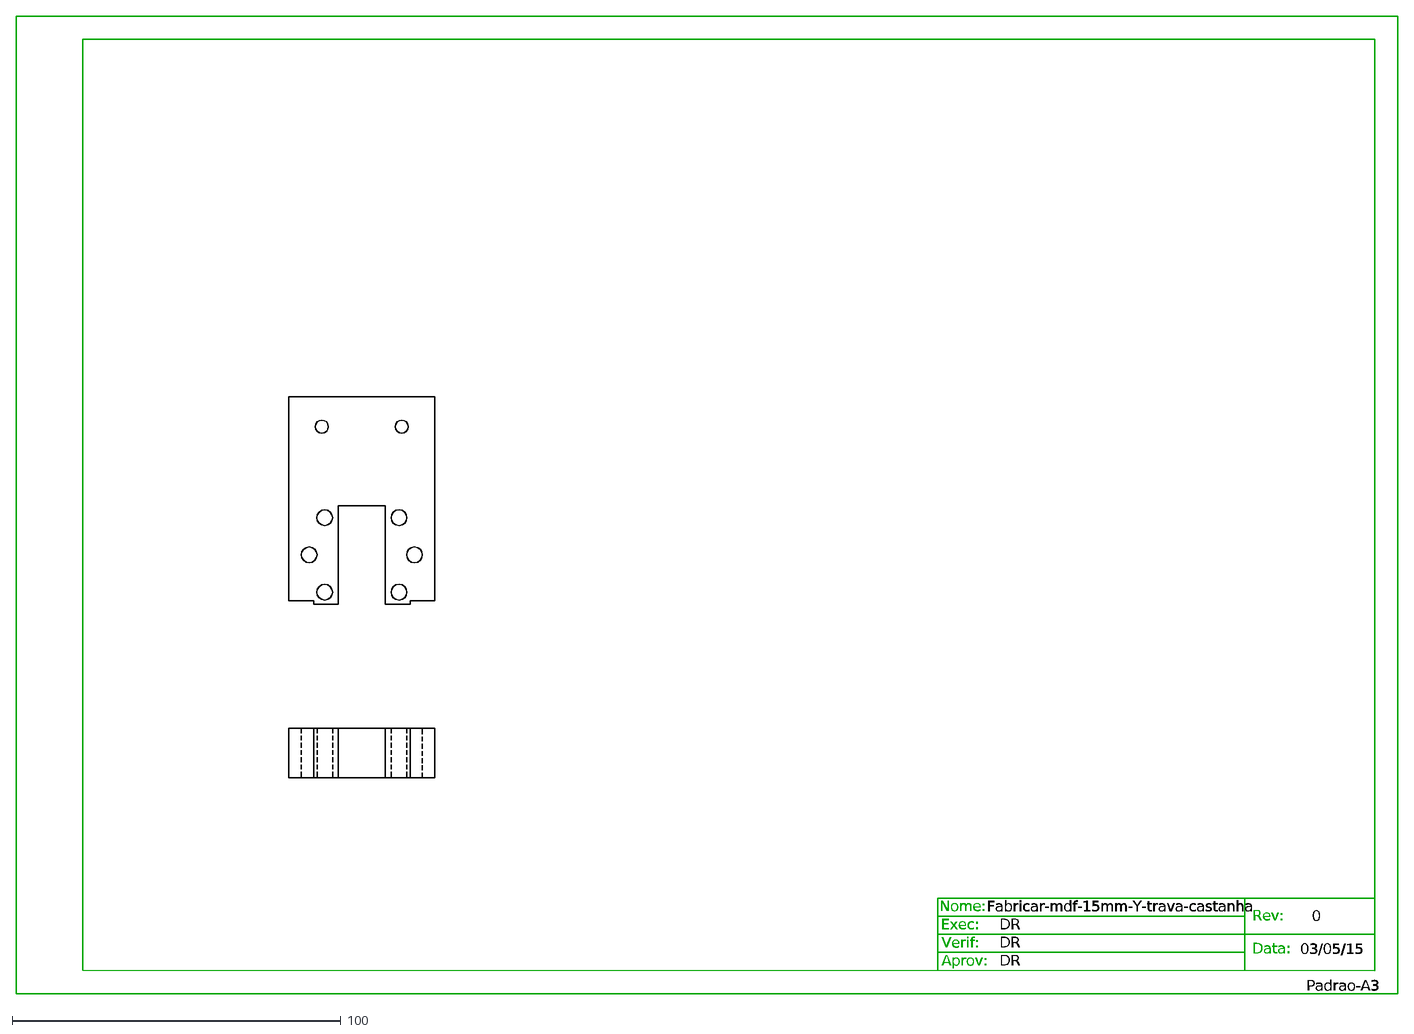
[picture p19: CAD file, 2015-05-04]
desenhos2D/Fabricar-mdf-15mm-Y-trava-castanha.dxf
Verif:
Exec:
Nome:
Rev:
Data:
Aprov:
DR
0
03/05/15
Fabricar-mdf-15mm-Y-trava-castanha
Padrao-A3

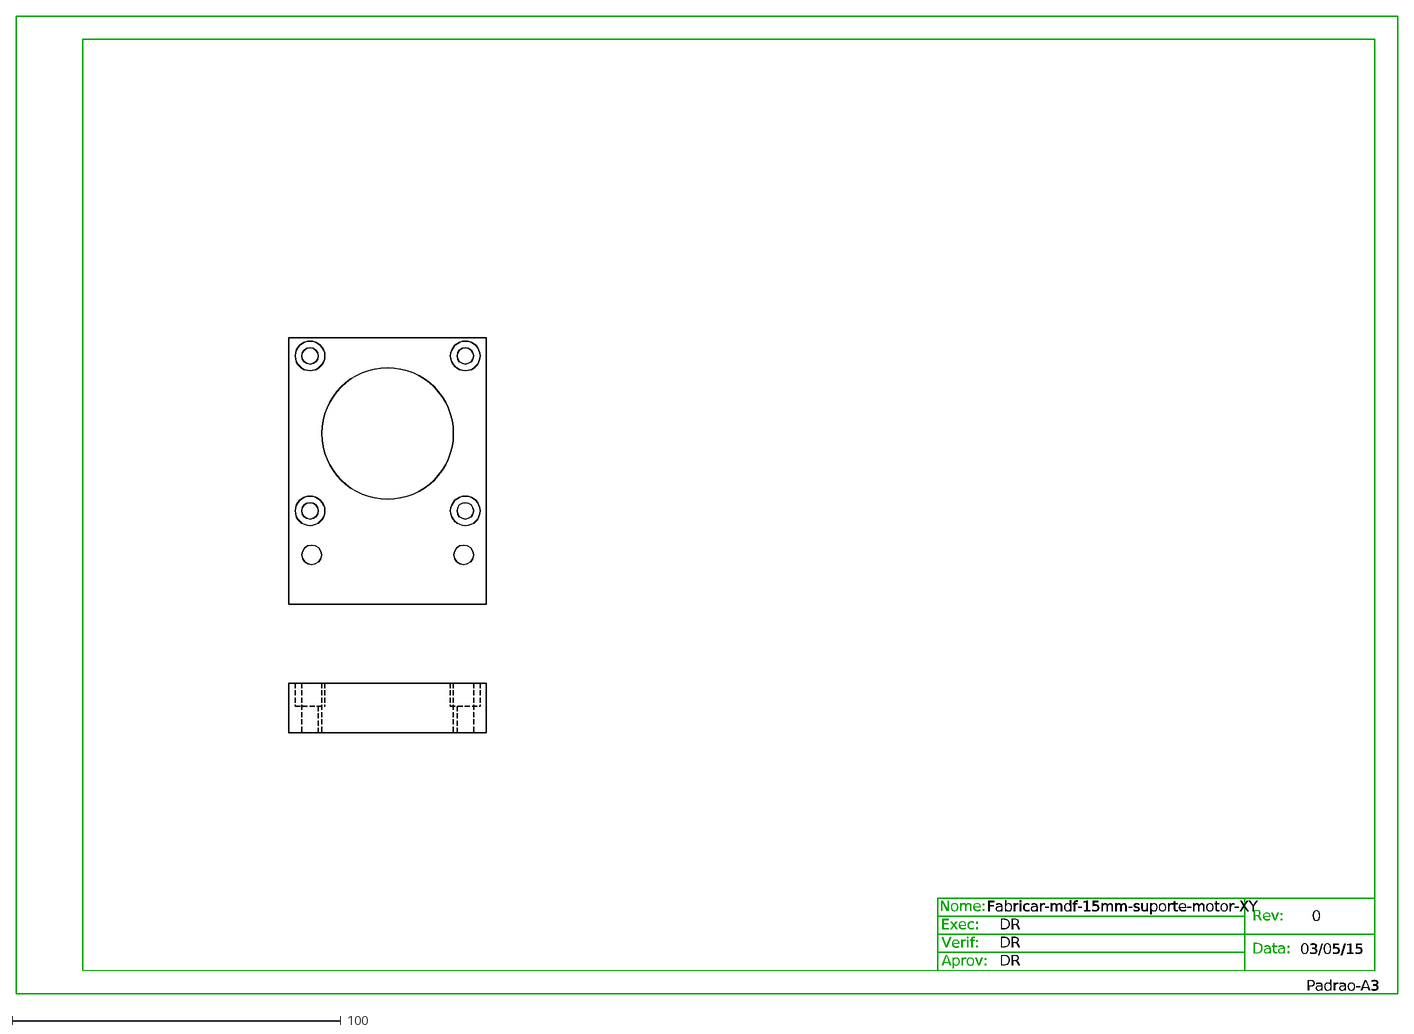
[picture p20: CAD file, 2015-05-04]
desenhos2D/Fabricar-mdf-15mm-suporte-motor-XY.dxf
Verif:
Exec:
Nome:
Rev:
Data:
Aprov:
DR
0
03/05/15
Fabricar-mdf-15mm-suporte-motor-XY
Padrao-A3

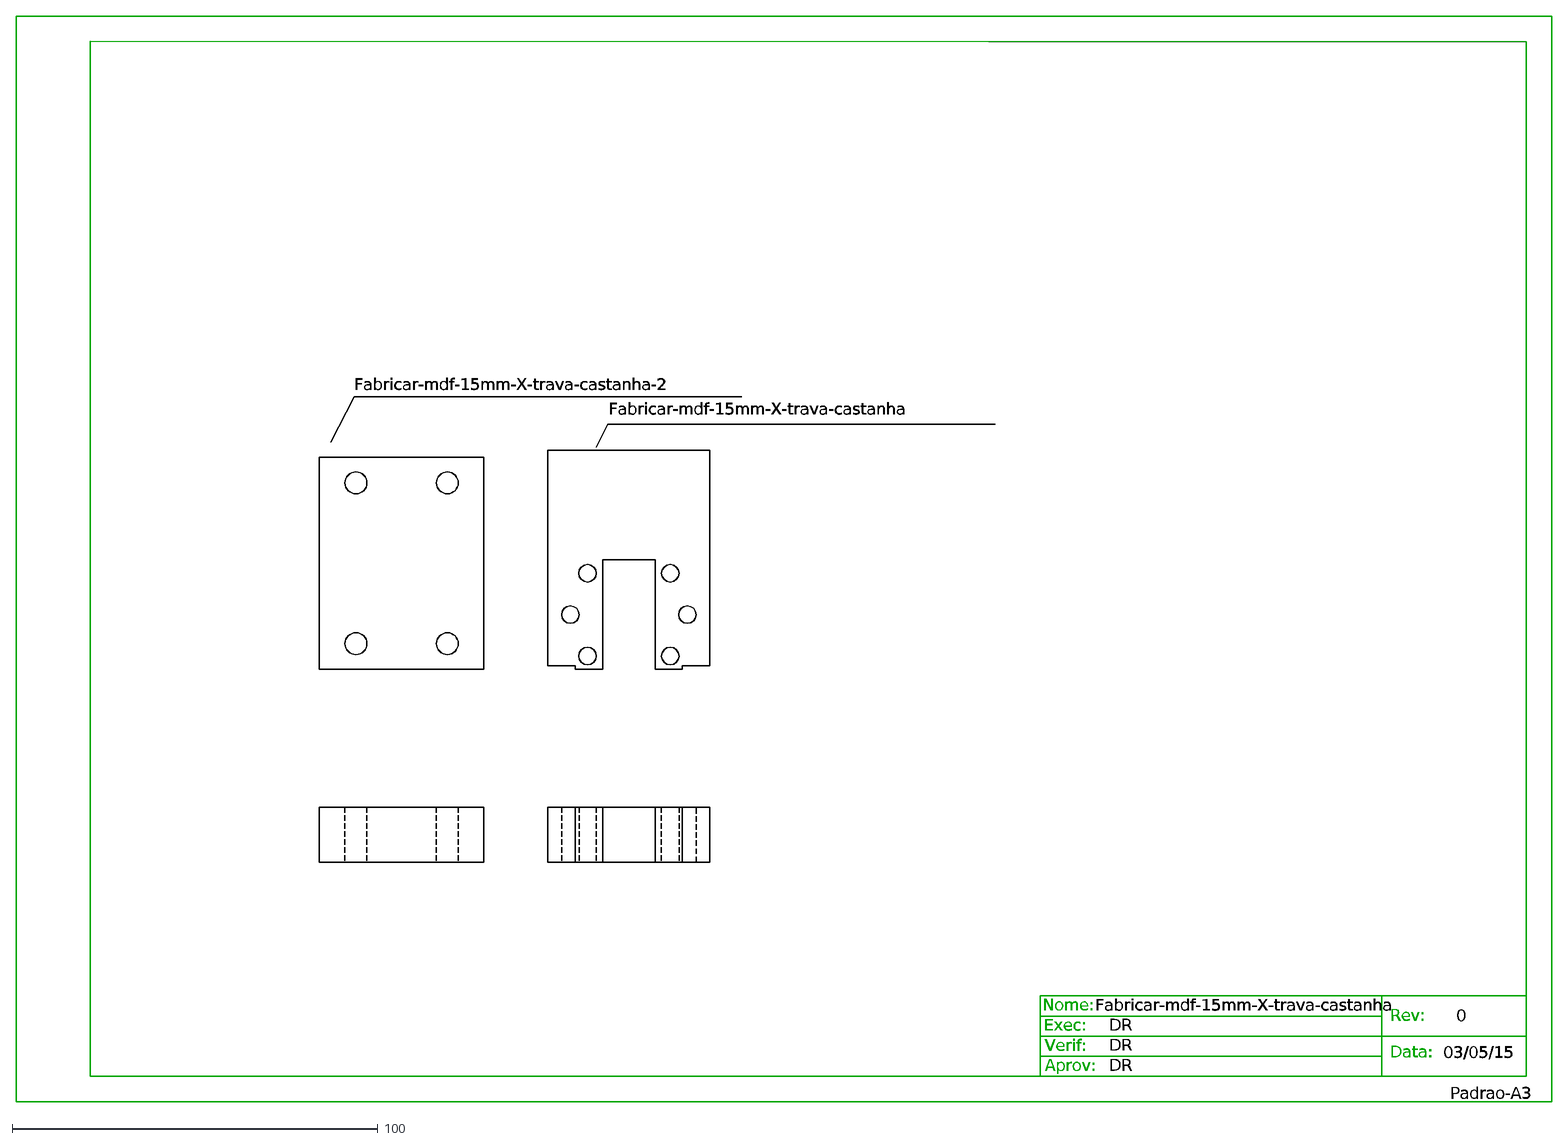
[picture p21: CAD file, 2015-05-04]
desenhos2D/Fabricar-mdf-15mm-X-trava-castanha.dxf
Verif:
Exec:
Nome:
Rev:
Data:
Aprov:
DR
0
03/05/15
Fabricar-mdf-15mm-X-trava-castanha
Padrao-A3
Fabricar-mdf-15mm-X-trava-castanha-2

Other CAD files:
desenhos2D/Fabricar-Y-mesa.dxf
desenhos2D/Fabricar-mdf-15mm-Z-mesa.dxf

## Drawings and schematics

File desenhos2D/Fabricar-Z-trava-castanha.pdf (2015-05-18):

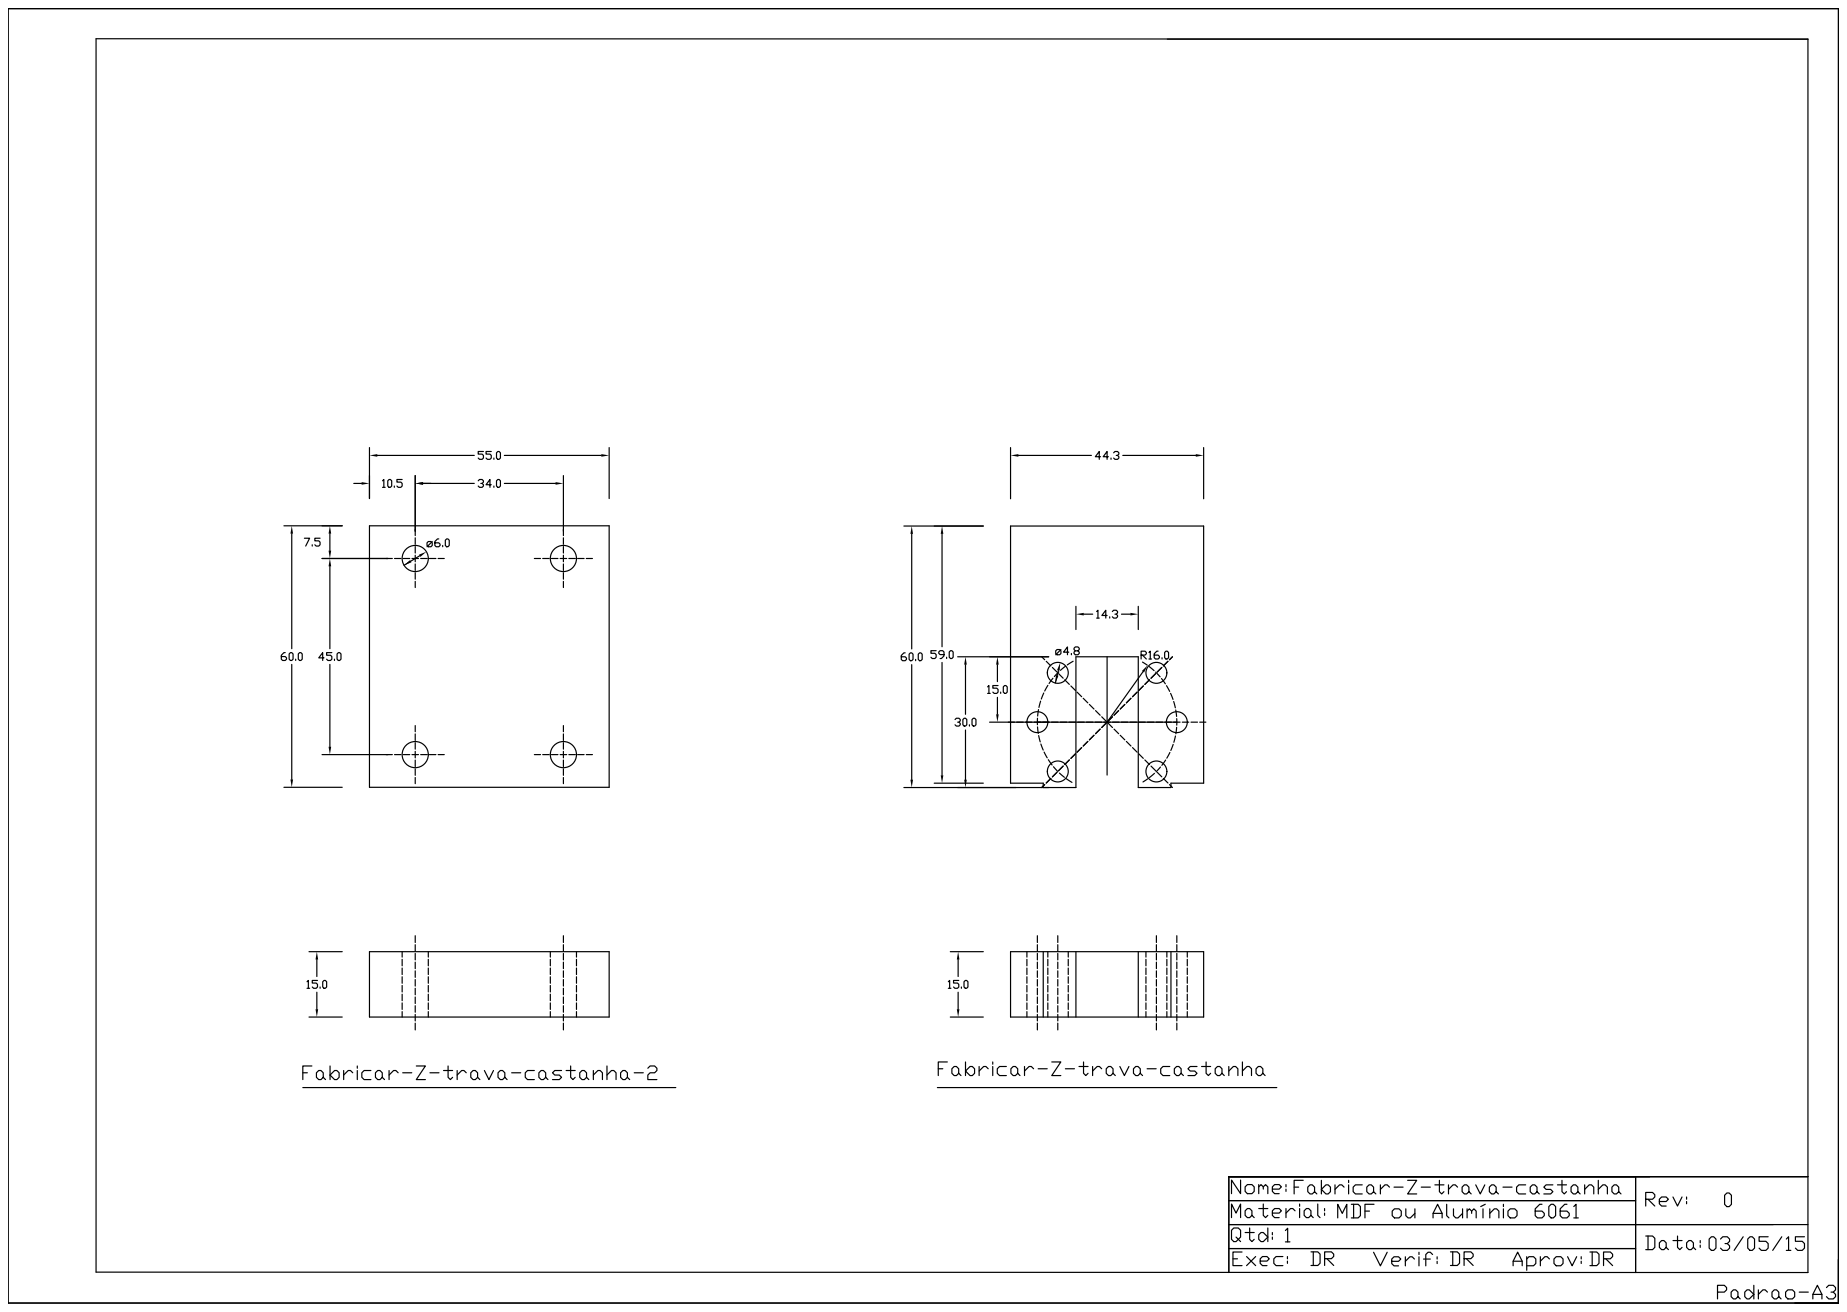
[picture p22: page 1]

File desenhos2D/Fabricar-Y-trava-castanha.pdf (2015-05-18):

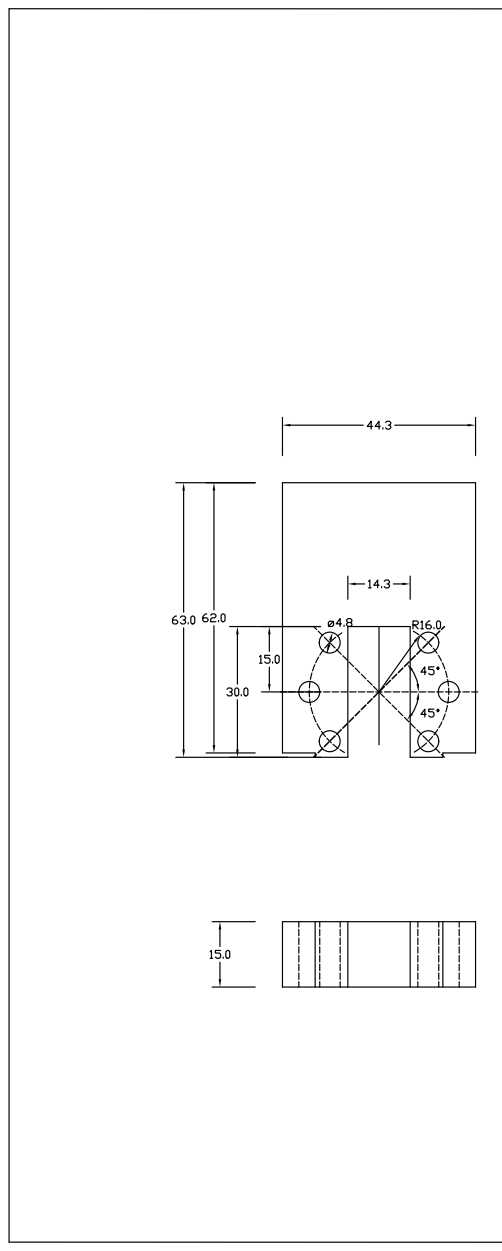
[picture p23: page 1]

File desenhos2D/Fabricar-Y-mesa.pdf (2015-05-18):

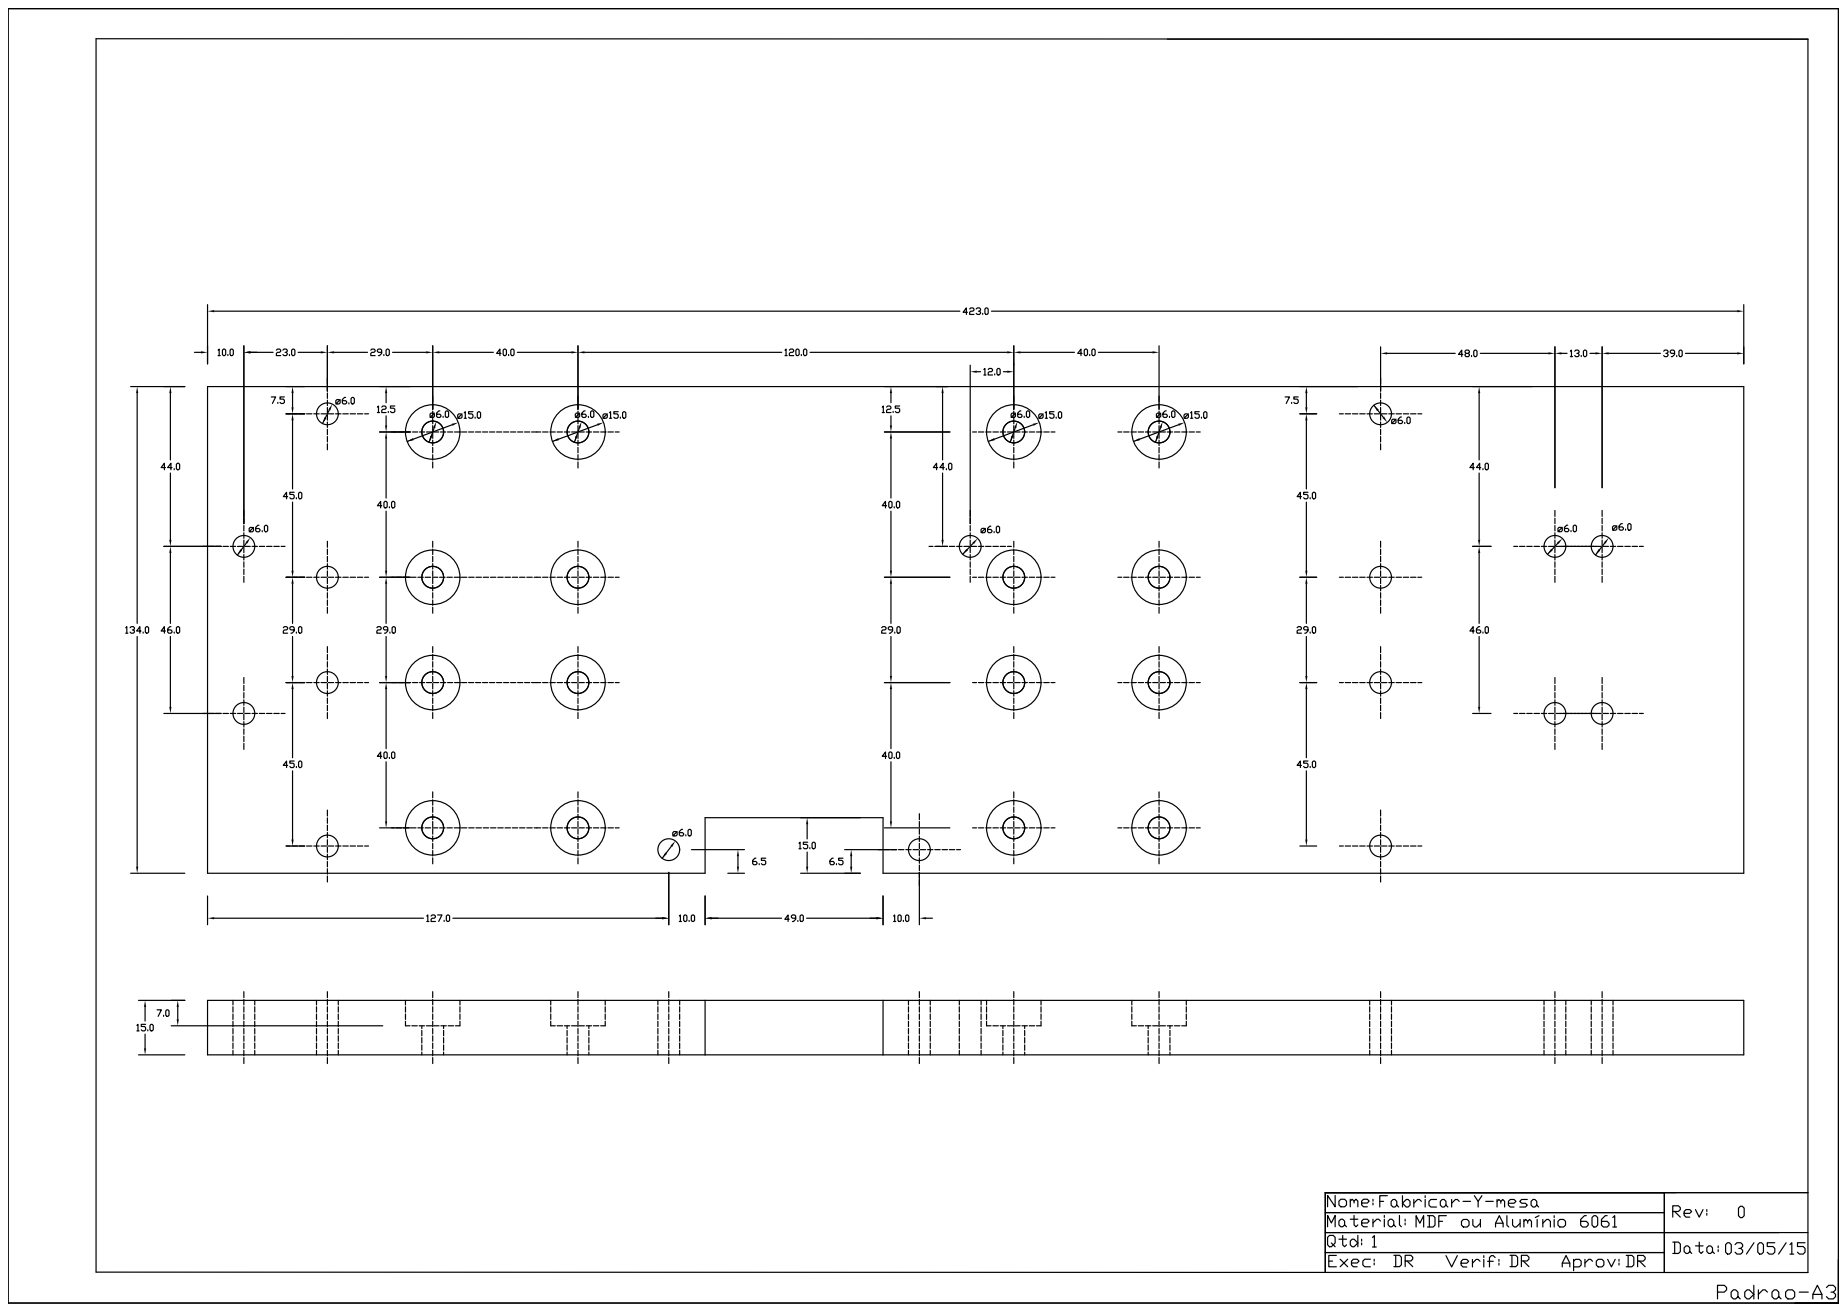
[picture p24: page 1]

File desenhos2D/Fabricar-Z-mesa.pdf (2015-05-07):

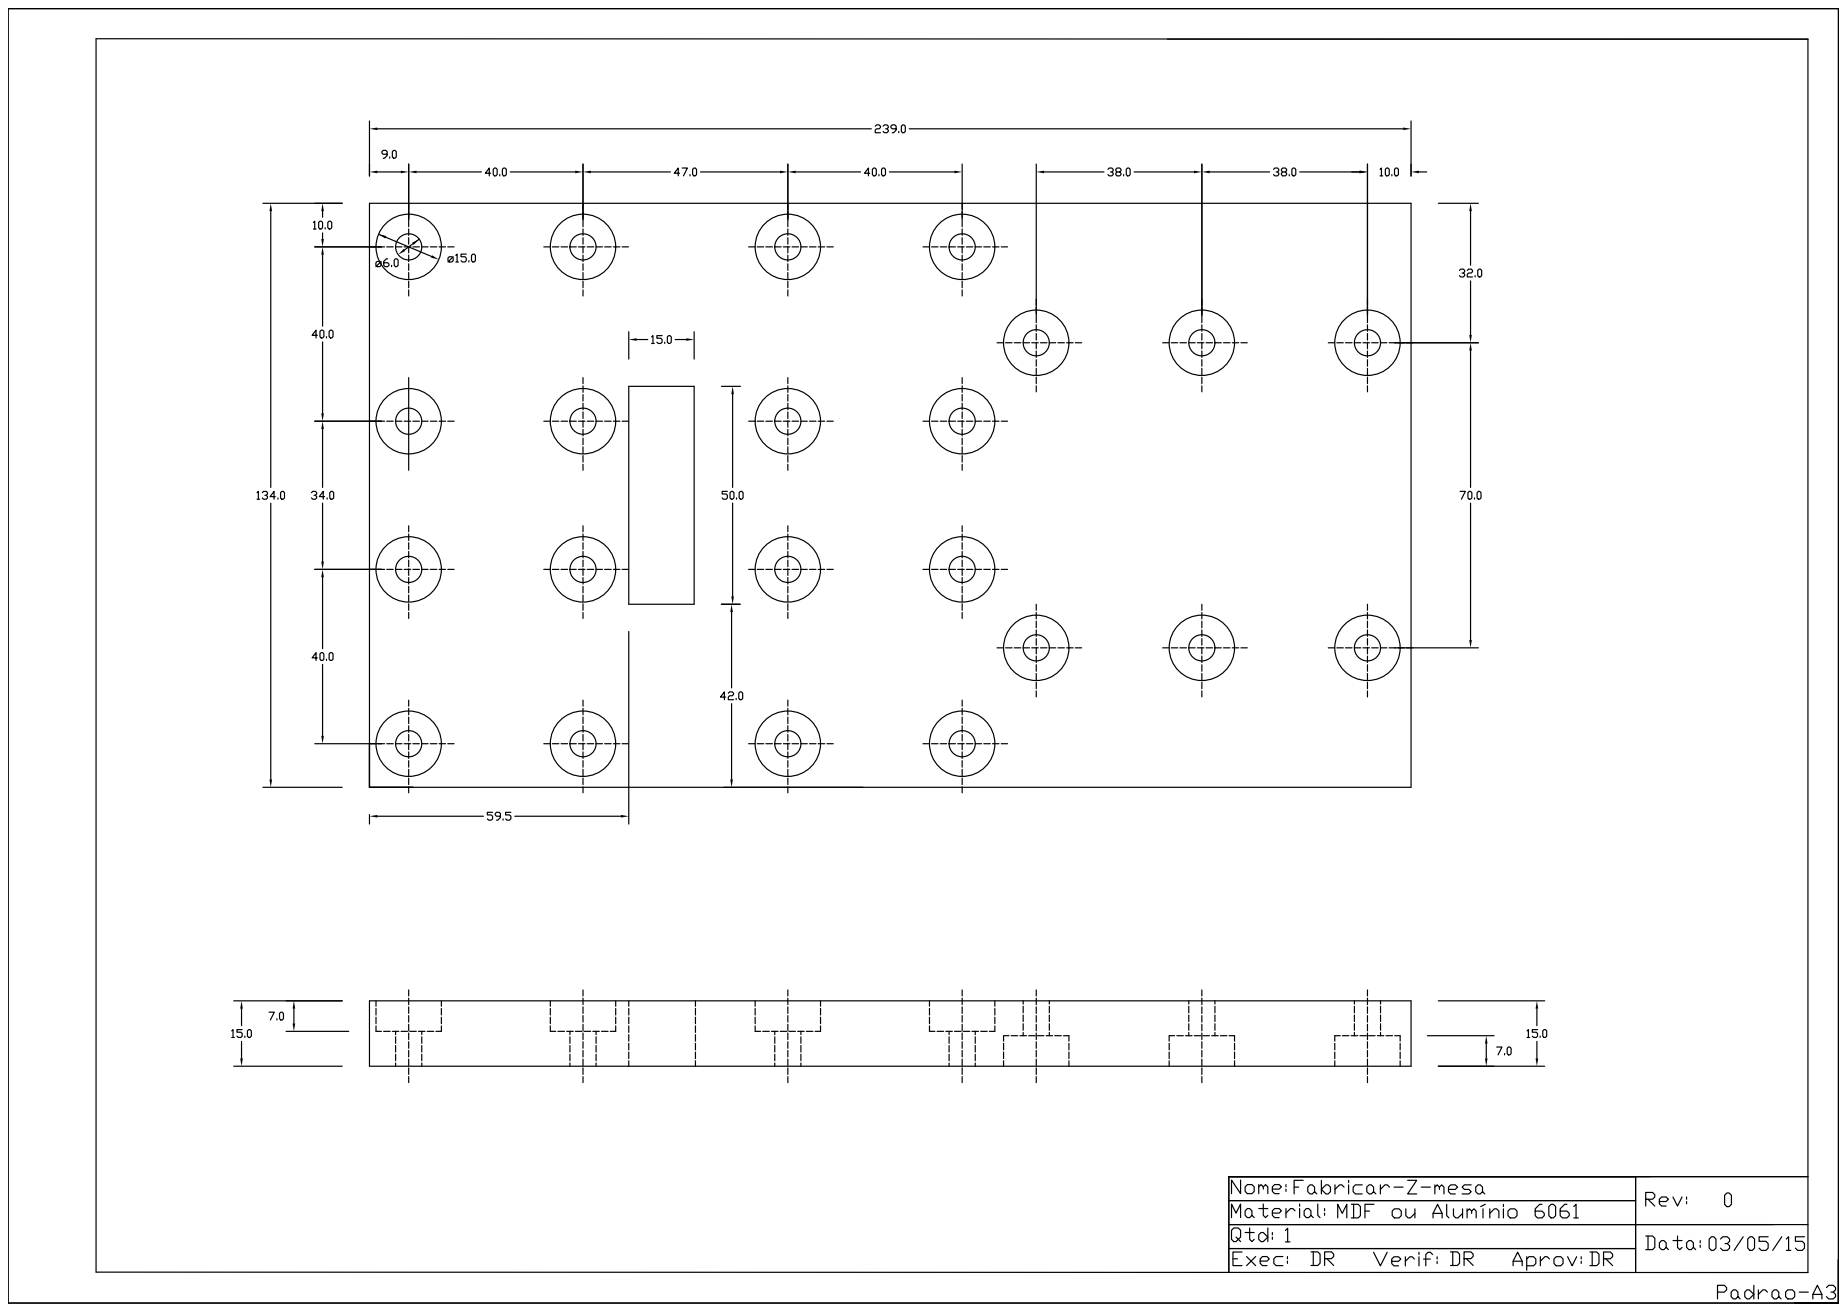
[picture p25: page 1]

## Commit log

2015-05-03 Lista de materiais
    inclusão da lista de materiais, ainda em versão preliminar.
    [BOM.xlsx]
2015-05-03 Inclusão do modelo 3D
    inclusão do modelo 3d e ajuste no nome do arquivo BOM
    [BOM.xlsx, CNCAlpha-BOM.xlsx]
2015-05-03 inclusao da imagem
    [CNCAlpha-BOM.xlsx]
2015-05-04 Carga dos arquivos 2d
    Carregamento dos arquivo 2d contendo os desenhos das peças a serem
    fabricadas. Desenho preparado para corte em CNC
    [Fabricar-mdf-15mm-X-mesa.dxf, Fabricar-mdf-15mm-X-trava-castanha.dxf, Fabricar-mdf-15mm-Y-trava-castanha.dxf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]
2015-05-04 atualização da lista de materiais
    [CNCAlpha-BOM.xlsx]
2015-05-04 revisao na lista de materiais e no readme
    [CNCAlpha-BOM.xlsx]
2015-05-04 atualização na descrição dos acopladores
    foi alterada a descrição dos acopladores
    [CNCAlpha-BOM.xlsx]
2015-05-04 Arquivo com os planos 2d geral movido para a pasta de desenhos2d
2015-05-04 carregamento de Gcode
    Gcode criado no CamBam
2015-05-04 carregamento de fotos
2015-05-04 inclusão do campo instruções para fabricação
2015-05-05 carregamento de informações dos eixos lineares
2015-05-07 Arquivos renomeados e melhoria nas inf. dos desenhos
    Os arquivos foram renomeados removendo o tipo do material do nome, já
    que no futuro estas peças serão de Alumínio.
    O carimbo do desenho também foi alterado recebendo o campo quantidade e
    tipo de material.
    [Fabricar-X-mesa.dxf, Fabricar-X-trava-castanha.dxf, Fabricar-Y-mesa.dxf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]
2015-05-07 Incluído cotas no desenhos
    Foram incluídas cotas no desenho para facilitar solicitação de
    orçamentos, não precisaria de cotas porque o objetivo é fabricar em um
    CNC.
    [Fabricar-Z-mesa.dxf]
2015-05-07 inclusão de valores aproximados Brasil e China
    [CNCAlpha-BOM.xlsx]
2015-05-18 Inclusão de cotas e criação de pdf
    Inclusão de cotas e geração de desenho em pdf para facilitar cotação do
    serviço de usinagem
    [Fabricar-Y-mesa.dxf]
2015-05-18 inclusão de cota geral
    incusão de cota com a dimensão geral da peça
    [Fabricar-Y-mesa.dxf]
2015-05-18 inclusão de cotas e criação de pdf
    Inclusão de cotas e arquivo pdf para facilitar a cotação para o serviço
    de usinagem
    [Fabricar-Y-trava-castanha.dxf]
2015-05-18 inclusão de cotas e criação de pdf
    Inclusão de cotas e arquivo pdf para facilitar a cotação do serviço de
    usinagem
    [Fabricar-Z-trava-castanha.dxf]
